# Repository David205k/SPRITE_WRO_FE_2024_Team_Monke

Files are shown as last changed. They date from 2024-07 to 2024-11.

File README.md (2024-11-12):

# SP RITE WRO FE 2024

## Team Information:


### Team ID:			`FE24_324_02`

### Team Name: 		`Team Monke` 

### Team Members: (from left to right)

- **Lim Jun Hong David <** [davidlimjunhong@gmail.com](mailto:davidlimjunhong@gmail.com) >
- **Chong Qi Yuan <** [Qiyuan146@gmail.com](mailto:Qiyuan146@gmail.com) >
- **Sachin Ilangovan <** [sachin5iconic@gmail.com](mailto:sachin5iconic@gmail.com) >

## Overview
#### Introduction	
Hello and welcome to Team `FE24_324_02` (Team Monke) GitHub repository. This is the GitHub repository for SINGAPORE World Robot Olympiad Future Engineers 2024. For WRO FE 2024, the competition focuses on Self-Driving Cars and in the challenge a robotic vehicle needs to drive autonomously on a parkours that randomly changes for each competition round.

In an ever-increasing automated world, the use of Autonomous Guided Vehicles (AGV) has become more prevalent. Furthermore, with recent improvements in Artificial Intelligence, specifically Computer Vision (CV), the integration of CV with AGVs is in high demand. Some possible applications with this integration include: 
-	Commercial: Self-Driving cars, housekeeping robots
-	Industry: Fully autonomous factory robots
-	Defence: Autonomous drones

This `README` will provide you with a quick overview of our process and resources we use for the competition. If you prefer a more thorough and detailed documentation of our journey for this competition, please check out our Engineering Journal that is also available in this GitHub repository `doc/`. Thank you

## Repository Content

- `doc/`:  Documentation
  - `Engineering Documentation.docx`
  - `Parts list`

- `models/`:
  - `Vehicle 3D Models` all ipt & iam files for vehicle design
    
  - `Engineering Drawings`
    - `Bottom Section Exploded view.png`
    - `Isometric view.png`
    - `Orthographic view.png`
    - `Top Section Exploded view.png`
    - `bottom disassembly.dwg`
    - `top disassembly.dwg`
    - `vehicle isometric view.dwg`
    - `vehicle orthogonal drawing.dwg`

  - `Disassembly Video`
    - `bottom disassembly.ipn`
    - `bottom disassembly.mp4`
    - `top disassembly.ipn`
    - `top disassembly.mp4`
  - `MONKE_BUST.stl`
  - `WRO_FE_2024.ipj.lnk`

- `ref/`: References for design idea & WRO_FE Rules, Field overview
  - `References.txt`

- `schemes/`: schematic diagrams of the electromechanical components illustrating all the elements used in the vehicle and how they connect to each other
  - `PCB Schematic Diagram.png`
  - `PCB ver.1.jpg`
  - `WRO_FE_PCB.fzz`
  - `WRO_FE_etch_copper_bottom.pdf`
  - `WRO_FE_schematic.fzz`
  - `front_PCB.png`
  - `Back_PCB.png`
  - `Soldered_PCB.jpg`

- `src/`: All python raspberry pi code to control software for all components
  - `main`
    - `main.py`
    - `pwmControl.py`
    - `tb6612fng.py`
    - `ultrasonicSensor_control.py`
  - `basic openCV/`:  basic programs using opencv and distance for objectDetection
    - `objectDetection.py`
    - `draw.py`
    - `read images.py`
    - `read videos.py`
  - `basic programs/`
    - `servo motor control ver.2.py`
    - `tb6612fng_motorDriver_control.py`

- `t-photos/`: 2 photos => Official Team photo and funny Team photo
  - `Official.png`
  - `Funny.png`

- `v-photos`: 6 photos of vehicle from all 6 side + overview for both SG and Türkiye Robot Designs
  - `WRO FE SG`  
    - `Top.png`
    - `Right.png`
    - `Left.png`
    - `Back.png`
    - `Front.png`
    - `Bottom.png`
    - `overview3.png`
  - `International Türkiye`
    - `Top.jpeg`
    - `Right.jpeg`
    - `Left.jpeg`
    - `Back.jpeg`
    - `Front.jpeg`
    - `Bottom.jpeg`
    - `Overview.jpeg`

- video: YouTube Video of vehicle demonstration in challenge
  - WRO FE SG
    - `Open Challenge.md`
    - `Obstacle Challenge.md`
  - International Türkiye
    - `Open Challenge.md`
    - `Obstacle Challenge.md`

- .gitignore: gitignore file
- README.md: This file

#### Hardware used
| Hardware | Description | Price (SGD)|
|---|---|---|
| Raspberry Pi 4 Model B | Control unit | $82.99 |
| MG996R Servo Motor | Steering actuator | $10.20 |
| 12v 380rpm 1.4kgcm Brushed DC Motor/ <br> DC 12V 1000RPM Gear motor | Main actuator | $19.64 |
| Full Metal Differential Gear set| Differential gear | $10.68|
| TB6612FNG Motor Driver | DC motor driver | $13.95 |
| LM2596 3A Buck Module with Display | DC voltage step down regulator | $4.96 |
| Raspberry Pi Camera Module 3 | Camera for Computer Vision | $46.61|
| US-015/ <br> VL53L1X Time of Flight sensor| High precision Ultrasonic Range Finder <br> / Long range, High precision IR Range Finder| $3.54 |
| HMC5883L | Triple Axis compass | $12.80 |
| Turnigy Lipo Pack 5000mAh 3S 25C W/XT-90/ <br> Turnigy Lipo pack 1300mAh 3S | Battery | $32.58 |
| 80mm Plastic Wheels SPG30/SPG50 | Main Driving wheel | $1.78 |
| Small Plastic Wheel | 34mm Steering Wheel | $2.00 |
| Ball Bearing | 6x13x5mm ball bearing | $3.41 |
| Printed Circuit Board | Custom PCB for mounting components | $8 |

For links to website for purchase of components, visit our either our /partslist or /engineering journal

## Overview of Robot
### WRO FE SG:
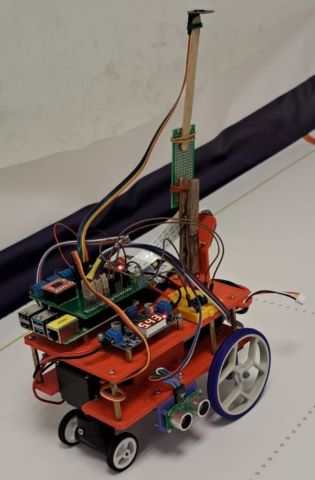
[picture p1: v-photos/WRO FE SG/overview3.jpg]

### WRO FE International Türkiye:
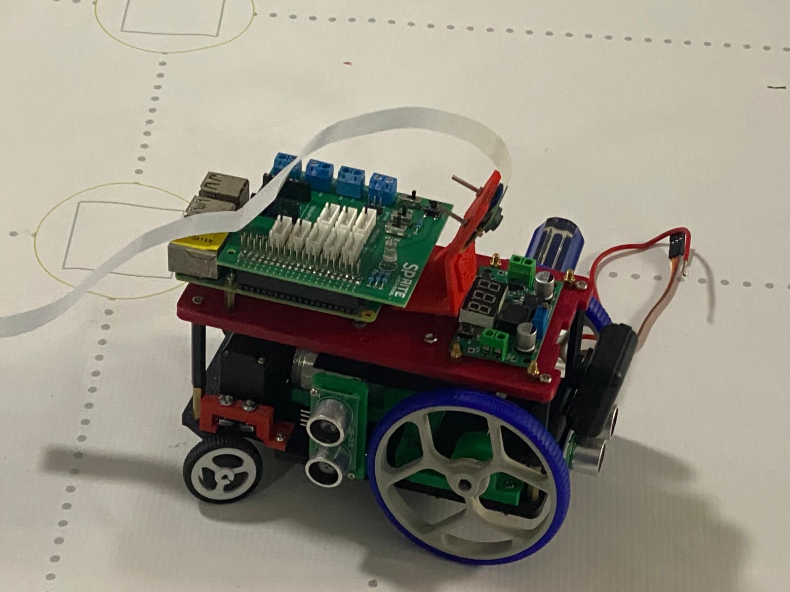
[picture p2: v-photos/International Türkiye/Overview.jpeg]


### Chassis
#### Steering
Originally, our robot featured a tricycle steering design. Where the steering is done directly by the servo turning (like a bicycle). This allowed us to simplify the steering design and also achieve tighter turns. 
However, we encountered some difficulties. Therefore we decided to swap to the ackerman steering for the internationals. 
This mainly offered advantageous in steering robustness, control and stability. However, this came at the cost of a more complex mechanism and a larger turning radius. 
#### Driving
Our robot is using a standard differential gear drive system, where 1 DC motor powers both wheels via a differential gear. A differential gear is used to prevent skidding and offer more stability and control. 

### Sense
Computer Vision: Our robot uses a Raspberry Pi to perform OpenCV computer vision to enable detection and avoidance of the obstacles. 
Distance Sensing: Our robot uses Time of Flight/Ultrasonic sensors to detect distances of walls, obstacles etc.
Vehicle direction: Our robot uses a Magnetometer Compass to obtain the bearing of the robot to enable accurate turns. 
By using this fleet of sensors, our robot is able to make informed decisions based on the information. 

For a more comprehensive overview of our design, proceed to our engineering document at `doc/`.

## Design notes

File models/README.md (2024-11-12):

This folder is dedicated to all hardware related CAD files. It is further split into 2 versions, the National and International version. 

This includes the Autodesk Inventor files and the STL files used for 3D printing components.

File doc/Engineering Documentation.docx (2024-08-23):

Team ID: FE24_324_02

Team Name: Team Monke

Team Members: Lim Jun Hong David, Chong Qi Yuan, Sachin Ilangovan

team monke engineering journal

WRO Future Engineers (FE)

ABSTRACT

The purpose of this competition is to design, fabricate, assemble, program, integrate and operate a self-driving car using computer vision.

This vehicle will be made using Raspberry Pi as its main controller and other off the shelf electronic components. The vehicle will also be operated as a steering robot, similar to real life cars.

Upon completion of this project, the vehicle should be able to navigate effectively between obstacles using sensor fusion and computer vision.

A copy of this Engineering Journal can also be found on GitHub (https://github.com/David205k/SPRITE_WRO_FE_2024_Team_Monke)

Other notes that we took are also found in the doc/ subdirectory.

1. Introduction
2. Design
- Hardware Overview
- Mobility Management
- Power and Sense
- Obstacle Management
- Code Style Guidelines
3. Fabrication
4. Assembly
5. Programming
6. Final Build
7. Conclusion

# Introduction

# System Architecture

## Hardware

## Software

# Development Process

# Results

# Conclusion

# References

# Appendix A

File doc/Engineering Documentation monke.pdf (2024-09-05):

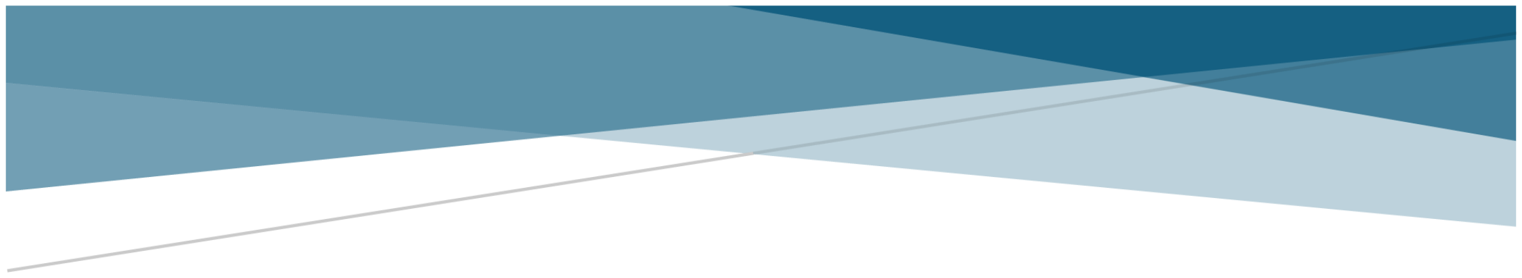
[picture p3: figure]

Team ID: | FE24_324_02
Team Name: | Team Monke

Team Members: Lim Jun Hong David, Chong Qi Yuan, Sachin Ilangovan

# TEAM MONKE ENGINEERING JOURNAL

## WRO Future Engineers (FE)

ABSTRACT
The purpose of this competition is to design, fabricate, assemble, program, integrate and operate a self-driving car using computer vision.
This vehicle will be made using Raspberry Pi as its main controller and other off the shelf electronic components. The vehicle will also be operated as a steering robot, like real life cars.
Upon completion of this project, the vehicle should be able to navigate effectively between obstacles using sensor fusion and computer vision.

A copy of this Engineering Journal can also be found on GitHub (https://github.com/David205k/SPRITE_WRO_FE_2024_Team_Monke) Other notes that we took are also found in the doc/ subdirectory.

## Contents

## INTRODUCTION

Project Background

In an ever-increasing automated world, the use of Autonomous Guided Vehicles (AGV) has become more prevalent. Furthermore, with recent improvements in Artificial Intelligence, specifically Computer Vision (CV), the integration of CV with AGVs is in high demand. Some possible applications with this integration include:

- Commercial: Self-Driving cars, housekeeping robots
- Industry: Fully autonomous factory robots
- Defence: Autonomous drones
Objectives

This project aims to create a self-driving car using Computer Vision via OpenCV and a Raspberry Pi camera. This will be assisted using Ultrasonic sensors to accurately identify distances. Furthermore, magnetometers will be used to determine the heading of the AGV to further refine turns overall sensor integration.
Scope of project

This project will be done using a Raspberry Pi. Therefore, design and fabrication of all components will be required. Integration of electronic components such as sensors, motor drivers, motors etc will also be required.

## HARDWARE

HARDWARE OVERVIEW

Description | Brand | Remarks | Quantity | Details
Servo Motor | | Steering Actuator | 1 | MG996R
12v 380rpm 1.4kgcm Brushed DC Motor | | Main Actuator | 1 | 12v 380rpm 1.4kgcm
Full Metal Differential Gear Set | | Differential Gear and Driver Gear for Robot rear shaft | 1
Raspberry Pi 4 Model B | Raspberry | Main Control Board | 1
High precision Ultrasonic Range Finder | | Ultrasonic Sensors | 3 | US-015
Raspberry Pi Camera Module 3 | Raspberry | Camera | 1
Motor Driver | | Motor Drivers | 1 | TB6612FNG
Ball Bearings | | Ball Bearings | 1 | 6x13x5 mm
Plastic Wheels | | Driving Wheels | 1 | 80mm
Small Plastic Wheels | | Steering Wheels | 1 | SPG330/SPG50 (80mm)
HMC5883L Module Triple Axis compass | | Triple Axis compass | 1 | HMC5883L
Lipo Pack | Turnigy | Power Supply | 1 | 5000mAh 3S 25C W/XT-90
LM2596 3A Buck Module with Display | | Voltage regulator | 1 | LM2596 3A
Custom designed PCB | | Integrate other components together | 1
NO Push button | | Push button to start/stop robot | 1
1k ohm resistor | | Resistor for push button | 1
220-ohm resistor | | Resistor for LEDs | 3

RGB cathode LED | RGB LED for display | 1
Switch | Turn on/off controller and motor | 2
Screw terminal | Connect battery and motor | 4

## OVERALL VEHICLE DESIGN

## Size

Our robot is at a shorter than the depth of the parking lot. This allows us to drive directly into parking, without the need to do parallel parking. A problem we encountered while doing such a design was that the physical components such as servo motor, differential gears and DC motor combined were too long. Therefore, we had to custom print a differential gear axle that was shorter.

## Component layout

Our robot has 3 layers available for mounting. The bottom layer is used mainly for actuation. The DC motor, differential and steering axle is at the bottom layer. Due to the large size of the batteries, the 2nd layer is dedicated to the batteries with a small part mounting the servo motor. The final top layer has the rest of our electronics such as the Raspberry Pi, the custom-made PCB, camera and voltage regulator. These components were placed here for easy access.

## MOBILITY MANAGEMENT

## Chassis

For our chassis, our team decided to use a tricycle approach instead of typical Ackerman steering configuration. This is reducing the steering mechanism’s complexity while also reducing turning radius. his approach simplifies the steering mechanism while significantly reducing the turning radius, allowing for sharper angles and tighter manoeuvrers. This is particularly useful in our scenario where obstacles and pillars are closely spaced, requiring the vehicle to make quick and precise turns in either direction. Our design deviates from traditional tricycle layouts by placing the steering mechanism at the rear and the differential gear system at the front. This configuration is intended to optimize the length of the robot while accommodating the ultrasonic sensors. One of these sensors is mounted at the front, where it benefits from existing space around the differential gear system. Placing the sensor here avoids the need for additional material spacing, which would have been necessary if it were positioned near the steering mechanism.
The rear-wheel steering allows the vehicle to pivot more sharply around the front wheels, making it extremely agile in tight spaces. This enables more precise adjustments when navigating through an obstacle course which is particularly useful when passing through obstacles.

## Steering

Using a tricycle approach, our vehicle uses a single steering axle, controlled directly by a servo motor. This allows us to simplify the steering design while also allowing a wide range of steering angles for optimal mobility.
The servo motor will be the steering mechanism of our vehicle. For our steering mechanism we only required the turning axle to turn about 90 degrees
The MG996R servo motor can rotate 90 degrees and has been tested to be more accurate than its previous models.

## Actuation

DC Motor & Full Metal Differential Gear Set:
At the start of planning and design we initially were planning on using a 3V - 6V Dual Axis TT Gear Motor but after some thought we realised that it would not be very efficient and logical as that motor would not have enough power to be able to move the vehicle at a required speed and would be very slow and would also be difficult to implement a differential gear set to it.

So, after some thought and research we landed on the 12v 380rpm 1.4kgcm Brushed DC Motor. From research, this motor provides higher speed and higher torque. The motor is mounted with a 30:1 gearhead that can produce 137mN.m torque with 380RPm rated 1A,12V. A full metal differential gear set is connected to the DC motor.

The use of differential gears allows the wheels to move at different rpms. They also serve a purpose of speed reduction while effectively transmitting torque. This allows smooth turning and cornering and optimal power distribution by dividing the force equally between them but still allowing them to follow paths of different length when turning.

The main function of the differential is to allow the wheels to turn at different rpms. In a scenario where the vehicle must turn right, the left wheel must move a longer distance than the right wheel, which means that the left wheel needs to rotate at a higher speed. This is where a differential would be useful.

DC Motor: | 137mNm, 380rpm
Mass of robot: | 1.45kg
| Torque/kg = 94.5mNm/kg
| Power to weight ratio = 1255W/kg
| Max speed of 380 rpm = 1591.7mm/s

The motor we chose provides sufficiently high RPM and torque whilst not being too expensive. Our needs as calculated above, are sufficiently met with a relatively controllable yet high max speed and sufficient power to weight ratio for a small robot.

Motor driver: TB6612FNG
To control our DC motor actuator, we require a motor driver. We chose the TB6612FNG since it met our power and actuation needs. It outputs 1.2A at up to 15V. This matches well with our motor which can take from 1A – 5A at 12V. This allows us to provide sufficient power to our motor while not overloading it or overspending on excessive equipment.
In addition to forward and reverse control, the TB6612FNG offers braking and standby modes. The brake mode quickly stops the motor, while the standby mode reduces power consumption when the motor is not in use.

## POWER AND SENSE

## Power

Consumption

DC motor: | 1A, 12V at max load
Raspberry Pi 4: | 5V, 3A
Battery: | 5000mAh 3cell 25C, 11.1v

At maximum load, the battery provides sufficient power with a comfortable excess. The main component consuming power is our controller, the Raspberry Pi at 3A. Power to the Raspberry Pi from the battery is first regulated by the Buck module to prevent overload. As for our main actuator, the DC motor, is controlled by the Motor driver which receives power directly from the battery. This is because the Motor Driver’s VM is rated at 15V, higher than the battery’s. This allows us to receive maximum power to the main actuator without any loss of power.

Servo Battery: | 1000mAh, 7V
Servo: | 7.2V max

We use a separate Servo battery since our main battery provides to much power to the servo even with a regulator.

## Sense

Controller: Raspberry Pi Module
We chose to use a Raspberry Pi instead of an Arduino because a Raspberry Pi is an operating system, allowing us to run more complex operations. Additionally, Raspberry Pi and Arduino are both popular choices in robotics projects, providing extensive online resources for support. We're also using VNC Viewer to remotely access and control the Raspberry Pi, which adds convenience and flexibility during development and testing. Moreover, since we plan to utilize the OpenCV library, which requires Python, Raspberry Pi is the ideal choice for our project.
- Processing Power: The Raspberry Pi 4 Model B is equipped with a quad-core ARM Cortex-A72 CPU, providing significantly more processing power compared to other microcontrollers like Arduino. This allows it to run complex algorithms, such as computer vision or machine learning, in real-time.
- Versatility and Flexibility: the Raspberry Pi 4 offers access to a vast ecosystem of software and programming languages. This flexibility enables easy integration with various sensors, cameras, and software libraries needed for advanced robotics tasks.
- Image Recognition with OpenCV: The Raspberry Pi 4 supports the Raspberry Pi Camera Module, which enables image recognition tasks. Coupled with OpenCV, a widely used library for computer vision, the Raspberry Pi 4 can perform real-time image processing, object detection, and visual navigation. This capability allows your robotic vehicle to recognize objects, track movements, and make decisions based on visual inputs, providing a significant advantage in a dynamic environment.
- Connectivity: Built-in Wi-Fi and Bluetooth on the Raspberry Pi 4 are crucial for wireless communication, remote control, or IoT integration, which is particularly useful in competitions for connecting multiple devices. This is especially useful when coding and troubleshooting.
- Multiple I/O Options: The Raspberry Pi 4 offers multiple GPIO pins, USB ports, and HDMI outputs, allowing for interfacing with a wide range of peripherals, sensors, and modules without needing additional hardware.
- I2C BUS connection: The Raspberry Pi 4 provides SDA and SCL connection for I2C. This is because both the Gyro (mpu6050) and Magnetometer (TB6612FNG) use I2C. By using the I2C bus, the gyro and magnetometer will have their unique I2C bus address, preventing data overlap. I2C is used for these components since it allows for data exchange between microcontrollers with minimum wiring. Ultrasonic Sensor: US-015
For our vehicle, we have strategically placed three ultrasonic range finders at the front, left, and right sides. These sensors play a crucial role in manoeuvring by helping the vehicle avoid obstacles like traffic pillars and maintaining a safe distance from the external and internal boundary walls of the field. The side sensors are particularly useful for detecting the side walls, ensuring the robot stays centred. At the front, we've positioned both a camera and an ultrasonic sensor to detect obstacles and measure distances effectively. We also place the Ultrasonic sensor below the robot so that it can reliably detect the walls.

We're using the US-015 model, which offers a measuring range from 2 to 400 cm with an accuracy of up to 1 mm. Its stability and consistency make it ideal for precise robotics operations like this one.

Camera: PI Camera
The Raspberry Pi Camera is mounted on the front top of the vehicle, serving as the 'eyes' of the robot. Its primary function is to detect obstacles and identify their colour, which allows it to send signals to the robot on which direction to turn. By placing the camera in this position, it optimizes the vehicle's ability to efficiently detect obstacles.

We chose the Raspberry Pi Camera Module 3 as it is the latest model, offering advanced features such as phase detection, which facilitates image recognition. This capability allows the system to differentiate between green and red pillars, guiding the vehicle's directional turns accordingly. Additionally, the camera supports various default modes, including 480p at 120 frames per second. With such a high frame rate, our robot can receive near-instantaneous information, ensuring responsive and accurate movement.

Magnetometer: HMC5883L Module Triple Axis compass

We are using the HMC5883L is a magnetometer sensorto derive the direction of our robot. This will enable the robot to be able to make more refined movements. For example, the robot will be able to determine how many rounds it has done.
The main reason we chose the HMC5883L was due to its accessibility and price and our usage purpose. A gyroscope was not suitable since we required a direction heading and a gyroscope would require algorithms and further modifications to achieve that. The HMC5883L allowed us to obtain the direction of the robot at a relatively low price.

Integration: Printed Circuit Boards
To integrate all our sensors and microcontrollers, we required something to combine them together and provide the necessary power with I/O connection. Therefore, we chose to use a custom printed PCB. Two other options were available to us as well. A breadboard or a perforated board. Breadboards was not a very long-term solution, and breadboard connections are not very secure, particularly on a moving robot. Not to mention mounting of the breadboard would also cause issues. Perforated boards offer more secure connections, but the soldering of all connections will be time consuming. Furthermore, we wanted a solution that could last and could be reused for other projects. Therefore, we chose to use a PCB since it allowed us to have secure connections, enable stacking of header pins on the Raspberry Pi and less soldering required. This also provided a valuable learning experience in how to PCB design.

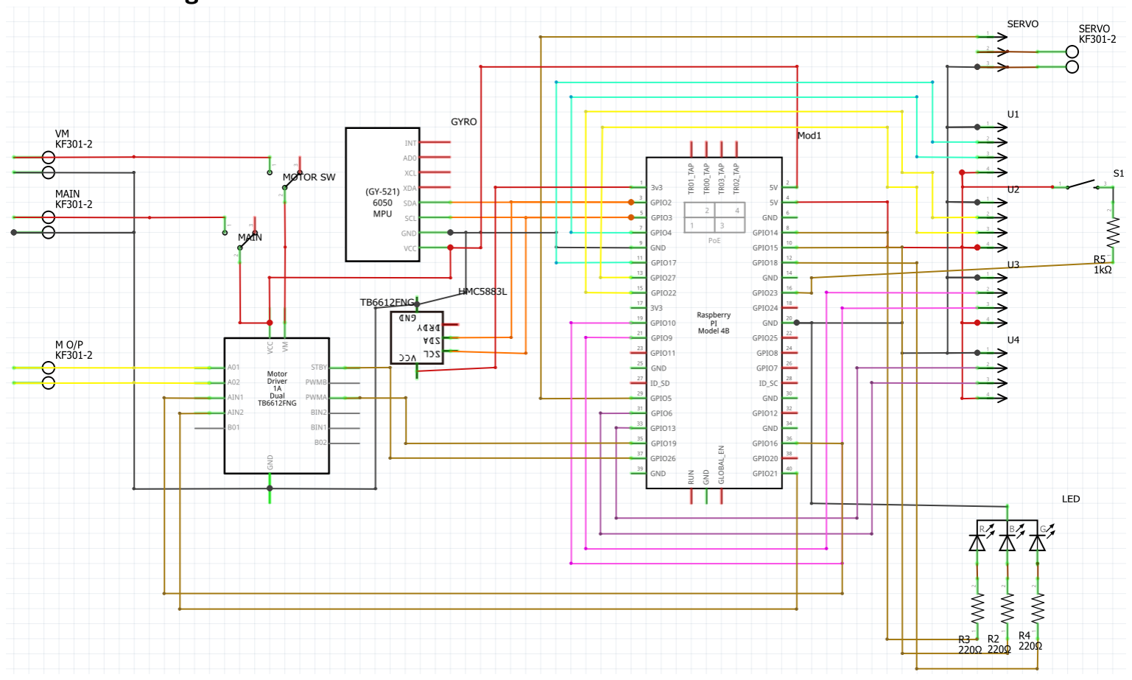
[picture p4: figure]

Schematic Diagram:

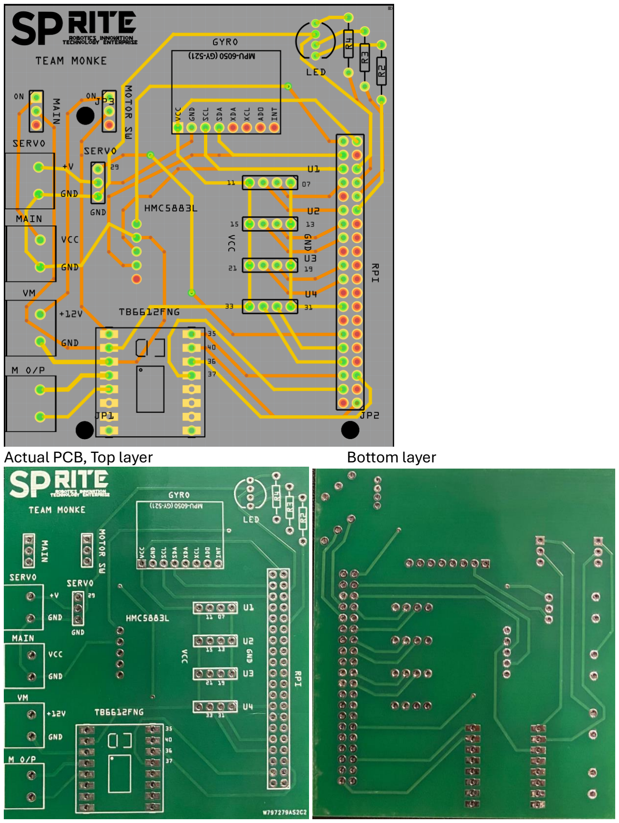
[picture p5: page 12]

Actual PCB, Top layer | Bottom layer

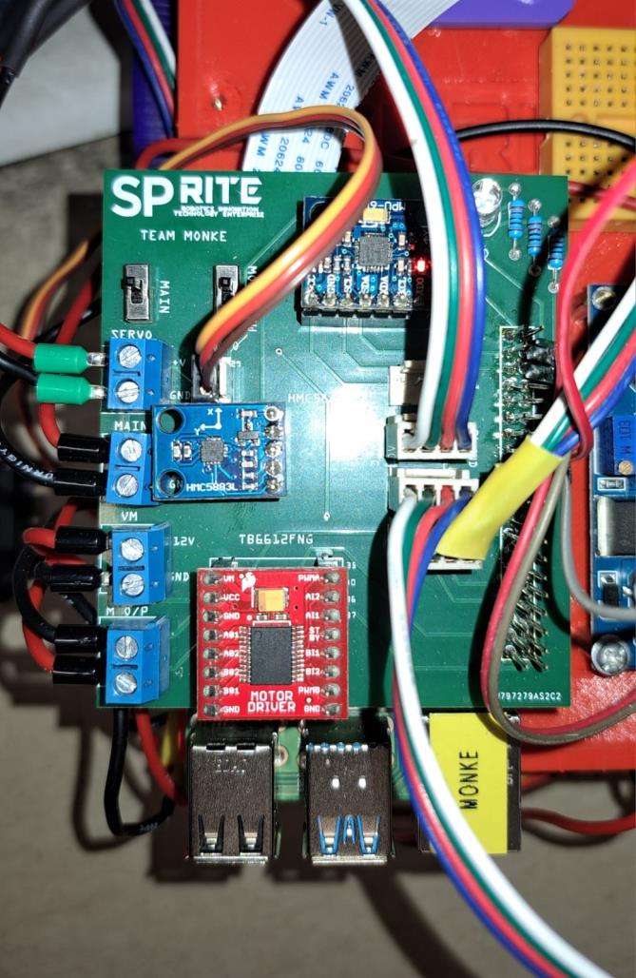
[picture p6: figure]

PCB with all components mounted on our robot

## DEVELOPMENT MILESTONES

## Fabrication

PCB

Old PCB
Visible from the image above, there were multiple improvements to be made to the PCB. For example, the screw terminals are the wrong size.

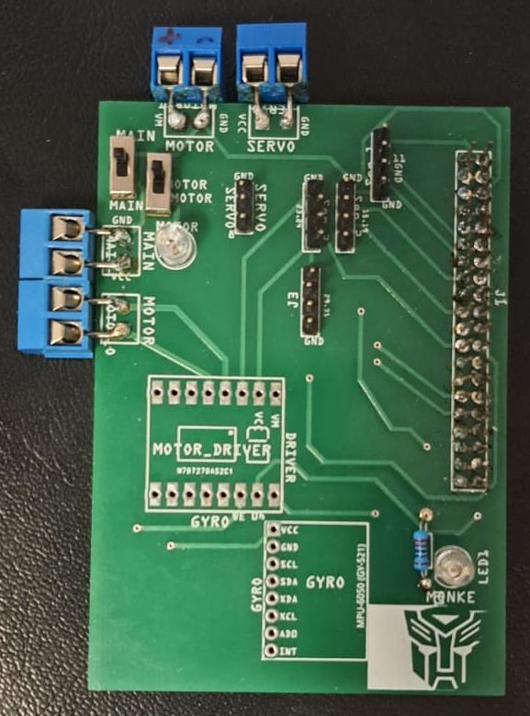
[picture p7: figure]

AGV

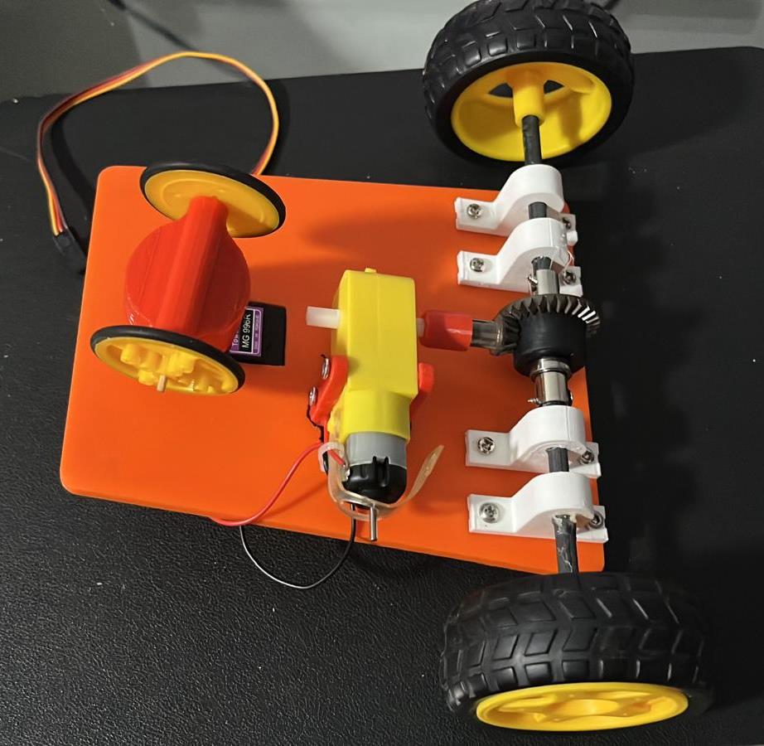
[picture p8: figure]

This is our very first AGV that we tried. This was meant as a proof of concept, testing out the differential gear drive and tricycle steering.

## Assembly

PCB
As our 2nd prototype, we used a breadboard to test out the motor driver. From insecure connections to messy wires, it was clear that we needed a PCB.

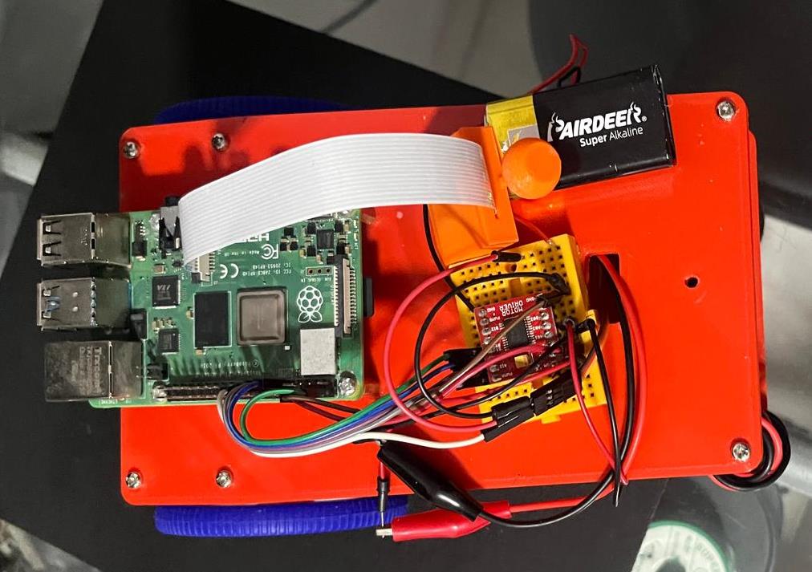
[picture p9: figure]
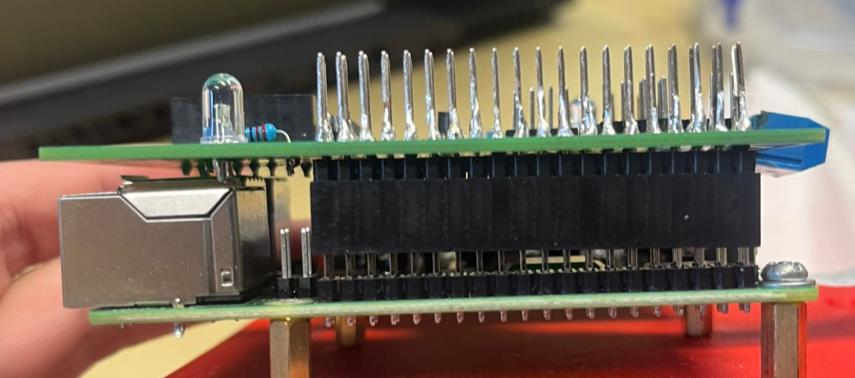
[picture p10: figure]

Upon assembling our PCB, we noticed that the Raspberry Pi’s USB and ethernet ports were blocking it.
AGV

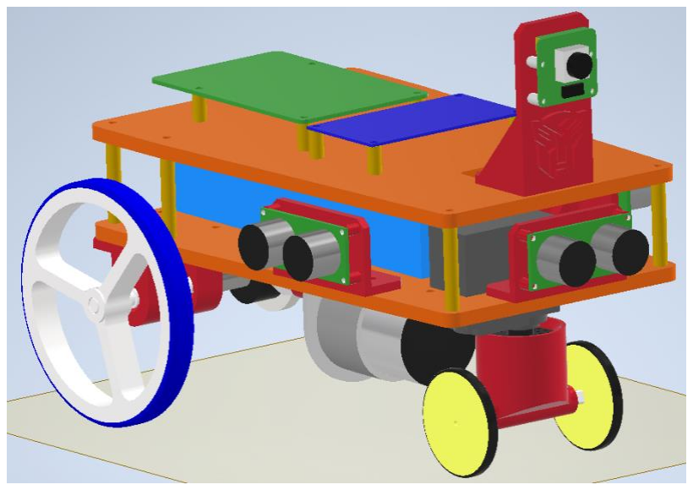
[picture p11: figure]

This is the 3D CAD file of our old AGV.
The robot is facing a different direction and is much longer than our current version.

As our final
prototype,
we started
integrating
the camera
and
OpenCV
control.

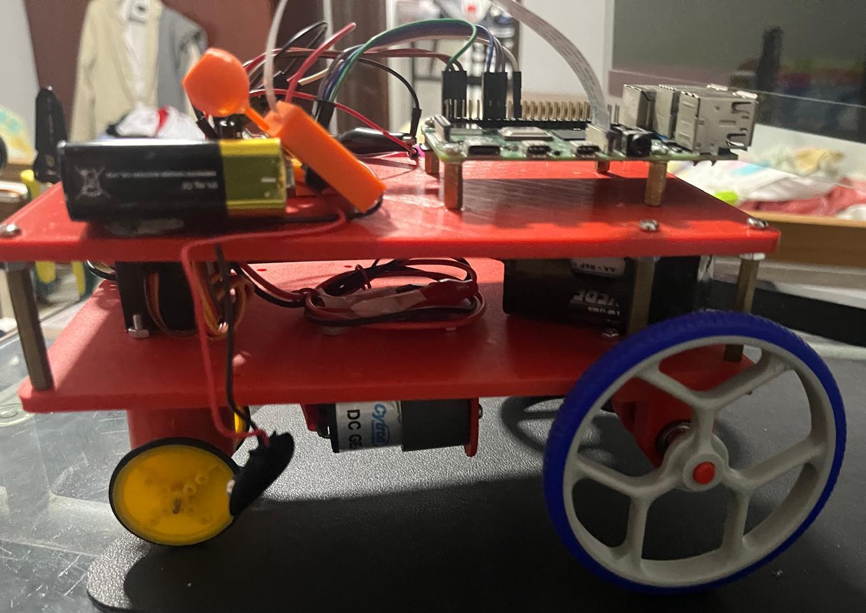
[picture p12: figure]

## Troubleshooting

Previously, we connected the servo motor directly to the battery. This caused the servo to overload and fry. Therefore, we are now using a smaller dedicated battery for the servo.
With our current steering configuration, our servo overload due to direct steering forces. When steering at sharp angles, the servo must exert a large amount of power and experiences forces of the robot pulling it forward.

## PSEUDO CODE

Open Challenge:

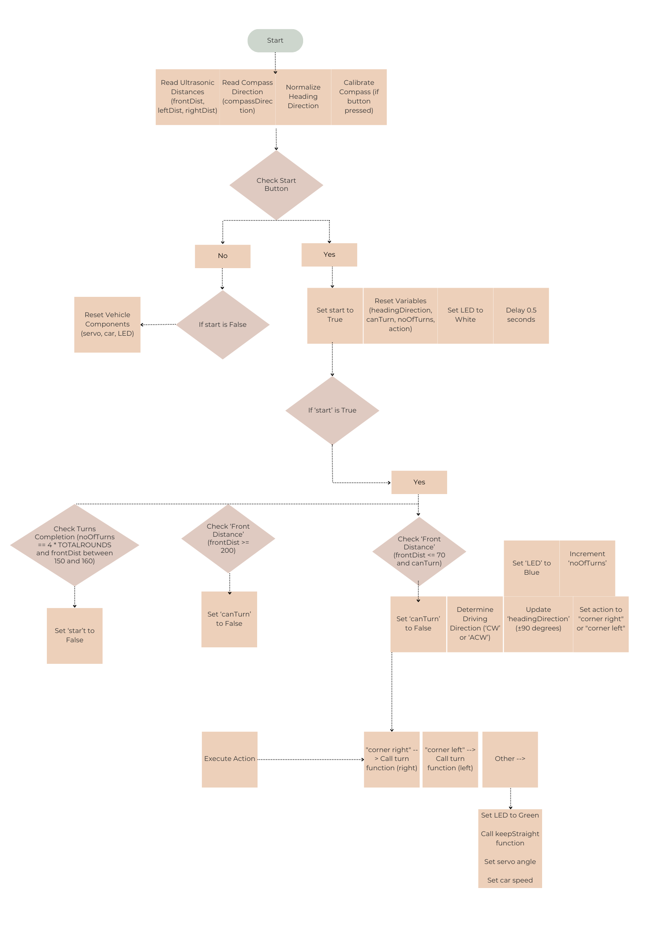
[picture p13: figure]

## CONCLUSION/IMPROVEMENTS

## Sensors

1) Instead of Ultrasonic sensors, we can use Lidar sensors instead. Lidar is much more consistent and accurate compared to ultrasonic sensors. Our team encountered some difficulties in the consistency of the Ultrasonic sensor.
2) A different camera can be used. Our current camera does not have very high frames at higher resolutions. This limits our object detection via computer vision.

## PCB

1) A push button can be added on the PCB so that we are able to start/stop the robot or give inputs during testing.

## REFERENCES

WRO FE Rule Book:
https://wro-association.org/wp-content/uploads/WRO-2024-Future-Engineers-Self-Driving-Cars-General-Rules.pdf (https://wro-association.org/wp-content/uploads/WRO-2024-Future-Engineers-Self-Driving-Cars-General-Rules.pdf)
VNC Viewer References:
https://www.google.com/url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 (https://www.google.com/url?rct=j&opi=89978449) https://youtu.be/ikUH_wOesIY?si=3h6Y2FHPOmsgjrJ-https://youtu.be/ocWZ9QFgvXk?si=nr7zo171_FX9tkB3
Programming References:
https://how2electronics.com/interfacing-hmc5883l-magnetometer-with-raspberry-pi/https://forum.arduino.cc/t/multiple-and-simultaneous-ultrasonic-sensor-controlling/26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 (https://forum.arduino.cc/t/multiple-and-simultaneous-ultrasonic-sensor-controlling/266009)
GitHub References:
https://github.com/World-Robot-Olympiad-Association/wro2022-fe-template

## APPENDIX A

Below are the images of our AGV
Bottom | Top

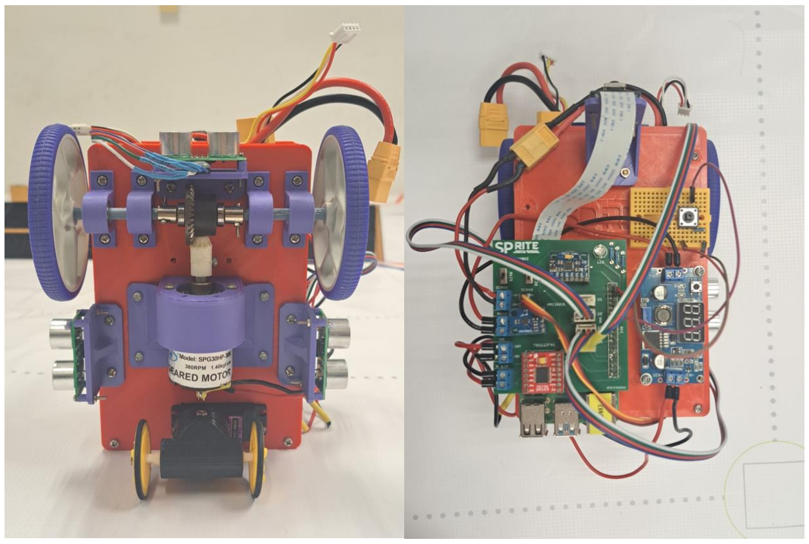
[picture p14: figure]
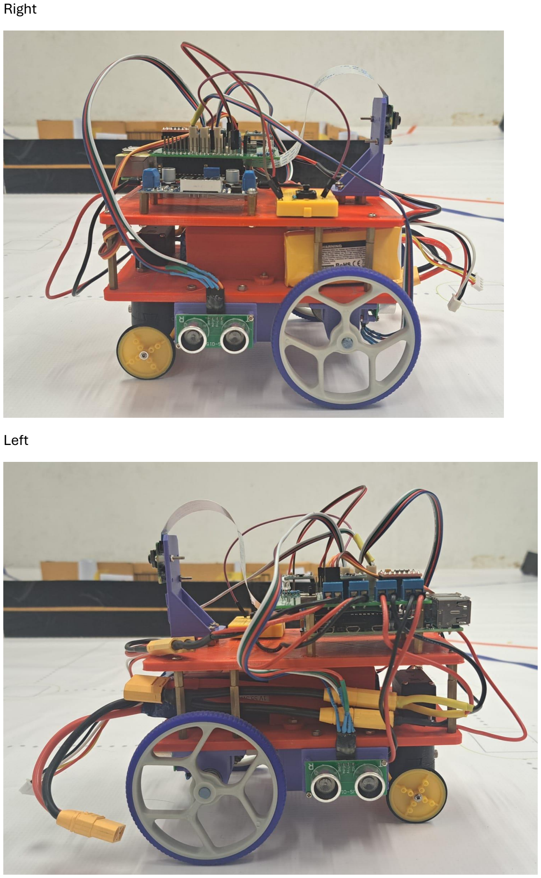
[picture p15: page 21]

Right

Left

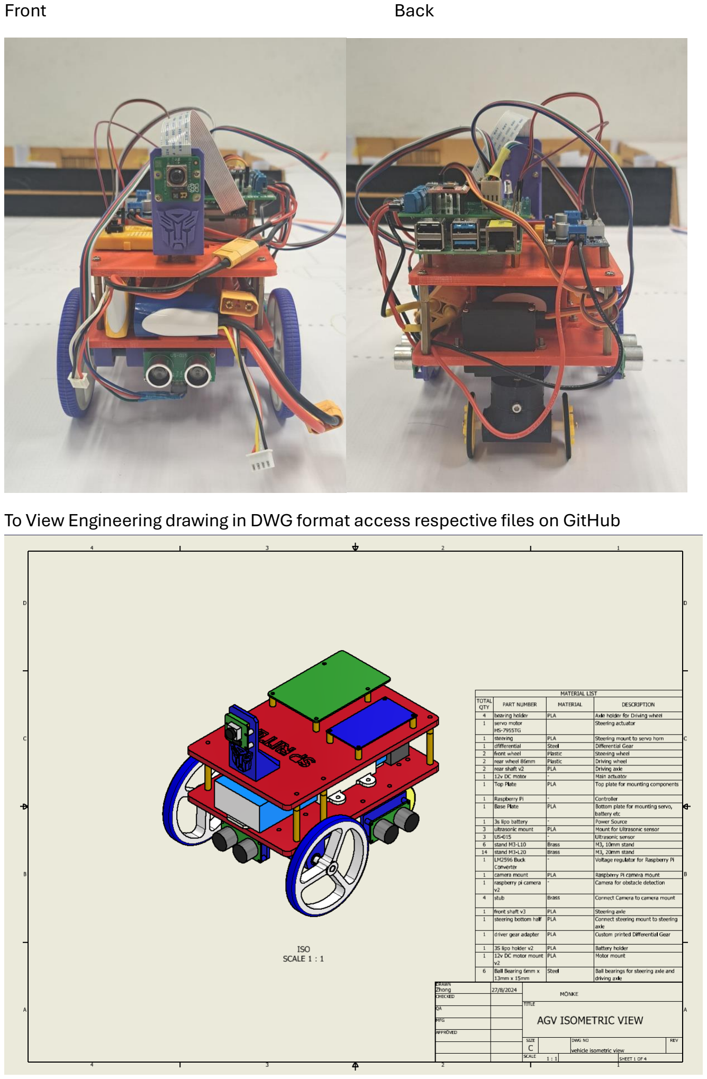
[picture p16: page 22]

Front | Back

To View Engineering drawing in DWG format access respective files on GitHub

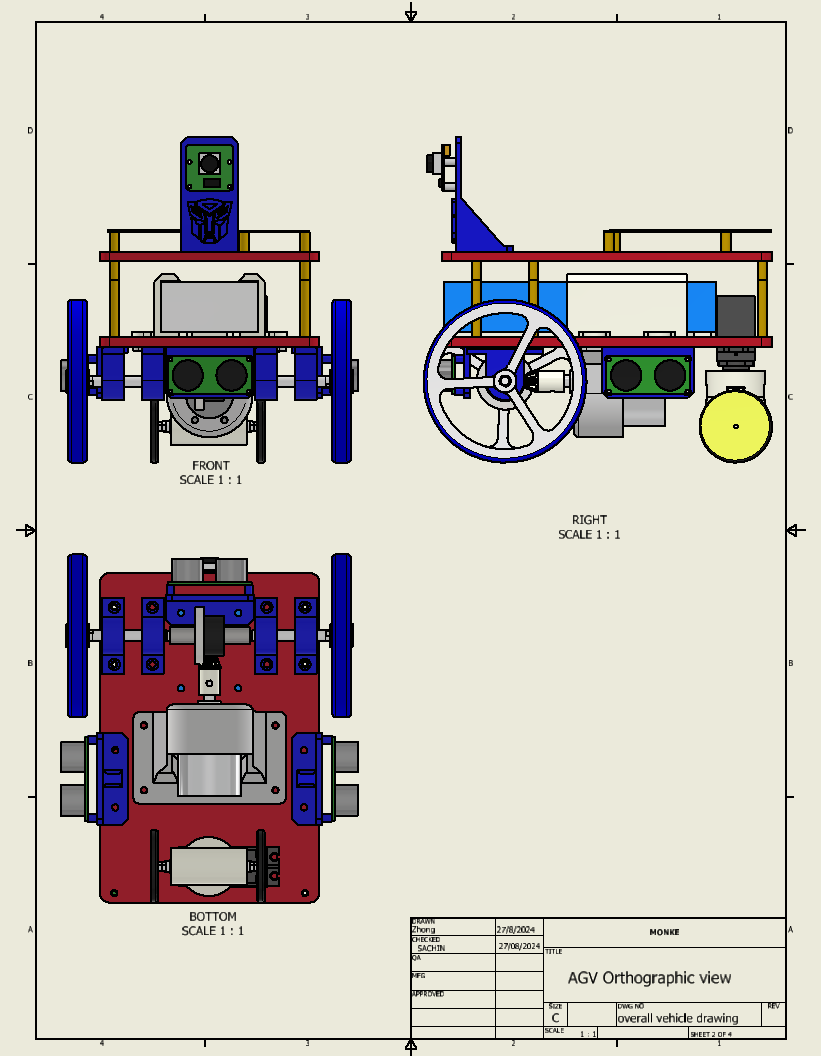
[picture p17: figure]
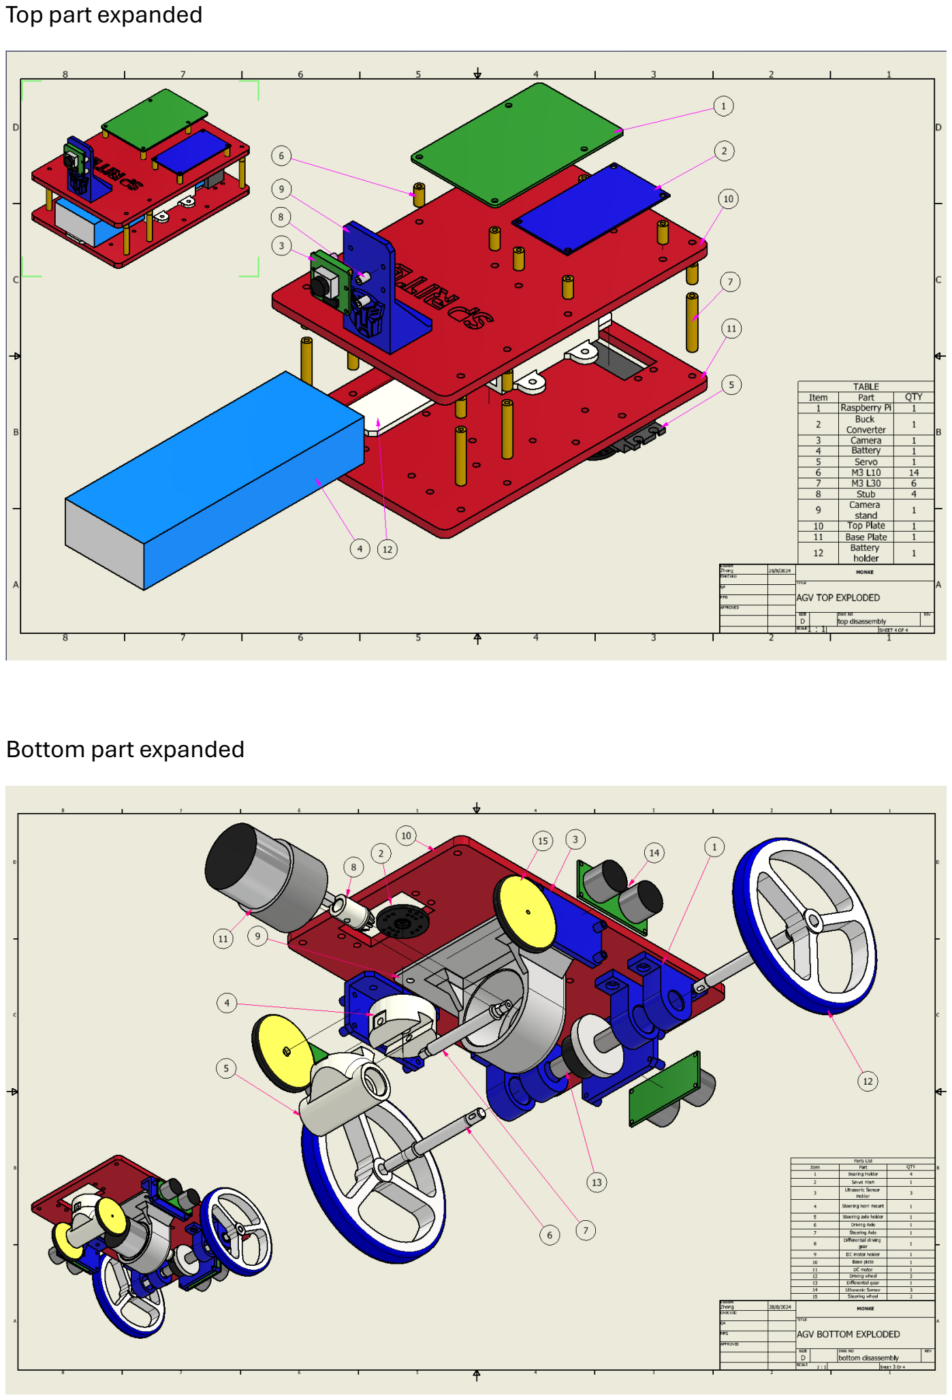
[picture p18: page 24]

Top part expanded

Bottom part expanded

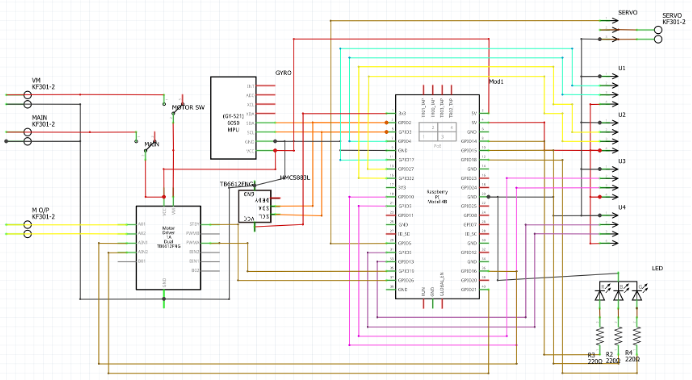
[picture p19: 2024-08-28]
schemes/PCB Schematic Diagram.png

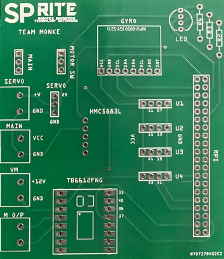
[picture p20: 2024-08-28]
schemes/front_PCB.png

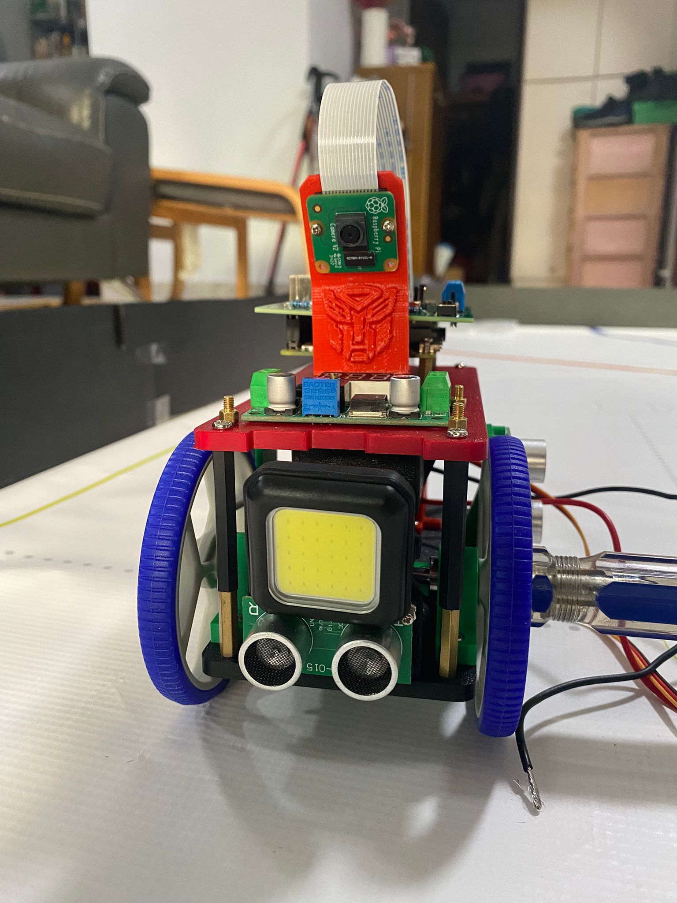
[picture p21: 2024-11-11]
v-photos/International Türkiye/Front.jpeg

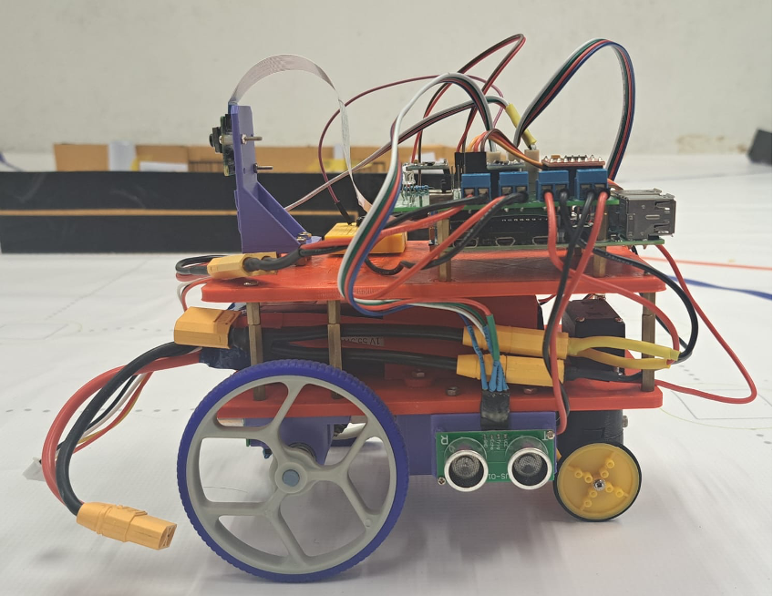
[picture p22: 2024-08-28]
v-photos/WRO FE SG/Left.png

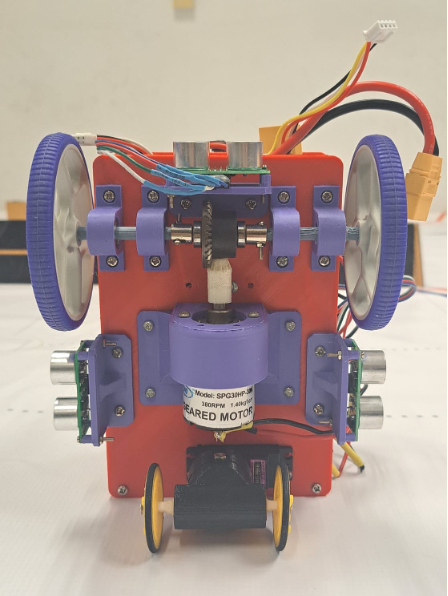
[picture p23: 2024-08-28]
v-photos/WRO FE SG/Bottom.png

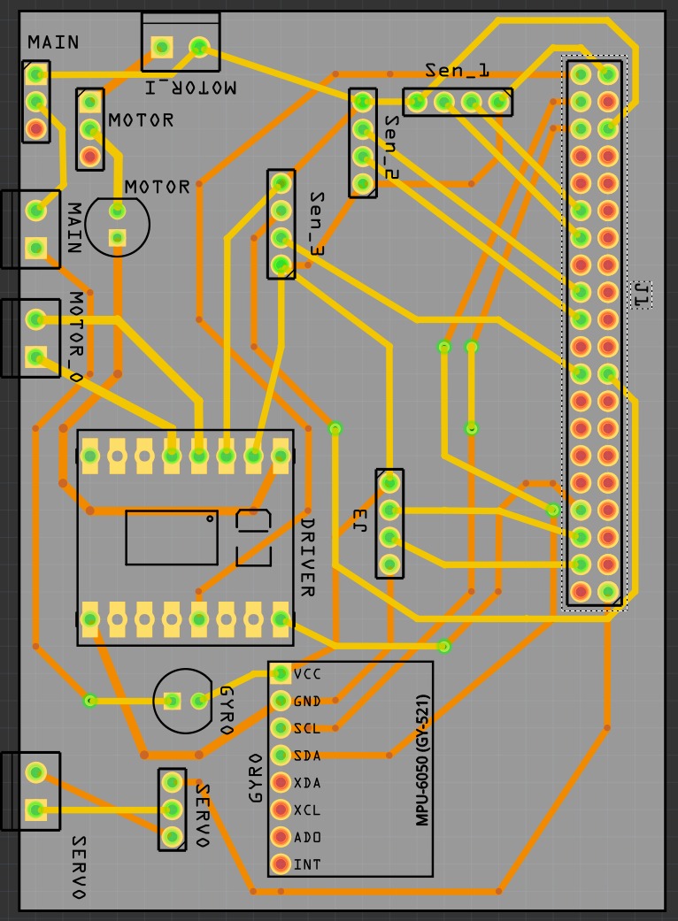
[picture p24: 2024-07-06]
schemes/PCB ver.1.jpg

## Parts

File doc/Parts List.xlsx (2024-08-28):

Description | Unit Price | Quantity | Source |  | Total Price | Remarks
12v 380rpm 1.4kgcm Brushed DC Motor | $19.64 | 1 | Cytron Tech | https://sg.cytron.io/p-12v-380rpm-1.4kgfcm-high-power-brushed-dc-geared-motor | $19.64 | Main Actuator
Servo Motor MG996R | $10.20 | 1 | Cytron Tech | https://sg.shp.ee/mt76Tnt | $10.20 | Steering Actuator
Full Metal Differential Gear Set | $10.68 | 1 | Shopee | https://shopee.sg/-Kesoto2-RC-Car-Differential-Replaces-Parts-Durable-Quality-Sturdy-Gear-Drive-Shaft-Spare-Parts-for-16101-16102Pro-16201Pro-Repair-Parts-Tru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 | $10.68 | Differential Gear and Driver Gear for Robot Rear Shaft
Raspberry Pi 4 Model B | $82.99 | 1 | Cytron Tech | https://sg.cytron.io/p-raspberry-pi-4-model-b-4-gb-and-kits | $82.99 | Main Control Board
5mp v1.3 Rapsbery Pi Camera | $6.99 | 1 | Shopee |  | $6.99 | 1st Camera Bought for Testing
TB6612FNG Motor Driver | $13.95 | 1 | SparkFun | https://www.sparkfun.com/products/14450 | $13.95 | Motor Drivers
High Precision Ultrasonic Range Finder US-015 | $3.54 | 4 | Cytron Tech | https://sg.cytron.io/p-high-precision-ultrasonic-range-finder-us-015 | $14.16 | Ultrasonic Sensors
Ball Bearings 6x13x5 mm | $3.41 | 1 | Shopee | https://shopee.sg/product/110868311/1947445015?d_id=a78bf&uls_trackid=501mi0gp009g | $3.41 | Ball Bearings
Front Wheels | $2.00 | 1 | Cytron Tech |  | $2.00 | Front Wheels
Plastic Wheel SPG30/SPG50 (80mm) | $1.79 | 2 | Cytron Tech | https://sg.cytron.io/p-12v-380rpm-1.4kgfcm-high-power-brushed-dc-geared-motor | $3.58 | Rear Wheels
HMC5883L Module Triple Axis Compass Magnetometer | $12.80 | 1 | Shopee |  | $12.80 | Compass 1
LM2596 3A Buck Module with Display | $4.96 | 1 | Cytron Tech | https://sg.cytron.io/p-lm2596-3a-buck-module-with-display | $4.96 | Voltage Regulator
Turnigy 5000mAh 3S 25C Lipo Pack W/XT-90 | $32.58 | 1 | HobbyKing | https://hobbyking.com/en_us/turnigy-battery-5000mah-3s-25c-lipo-pack-xt-90.html | $32.58 | Power Supply
GY-521 MPU6050 6DOF Accelerometer + Gyro | $3.75 | 1 | Cytron Tech | https://sg.cytron.io/p-gy-521-mpu6050-6dof-accelerometer-plus-gyro | $3.75 | Compass 2
Raspberry Pi Camera Module 3 | $46.61 | 1 | Cytron Tech | https://sg.cytron.io/p-raspberry-pi-camera-module-3-12mp-with-auto-focus-lens | $46.61 | Camera
TCS3200 Colour sensor | $11.79 | 1 | Cytron Tech | https://sg.cytron.io/p-colour-sensor-module | $11.79 | Colour Sensor
Custom designed PCB |  | 1
Noramlly Open Push button |  | 1
1k ohm resistor |  | 1
20 ohm resisior |  | 3
RGB cathode LED |  | 1
switch |  | 2
XT90 Connectors |  | 4
XT60 Connectors |  | 1
Total Cost (Excluding Shipping) |  |  |  |  |  | $280.09

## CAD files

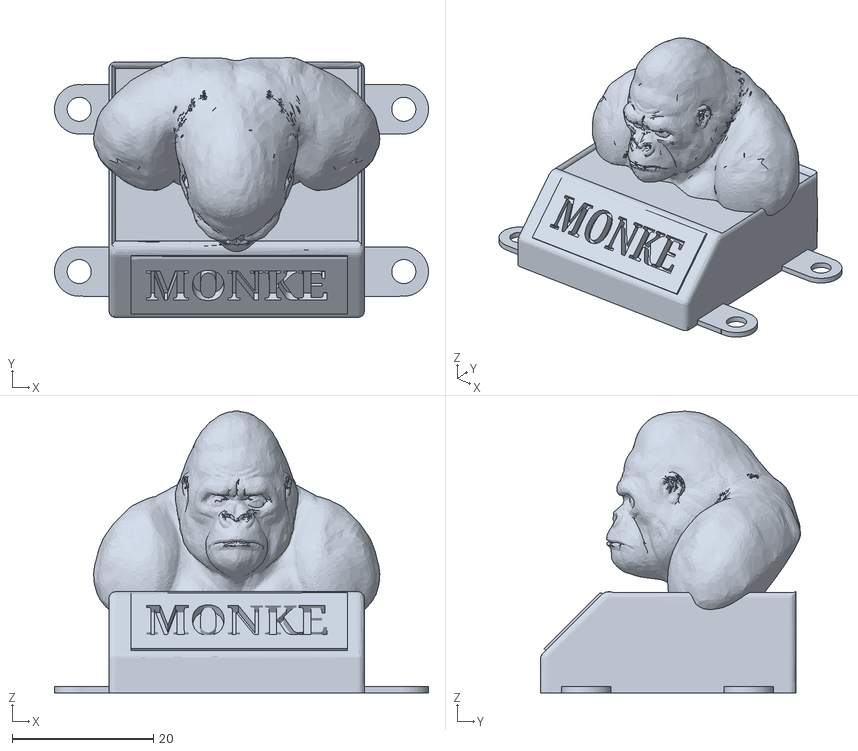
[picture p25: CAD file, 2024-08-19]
models/MONKE_BUST.stl
53.0 x 36.8 x 39.9

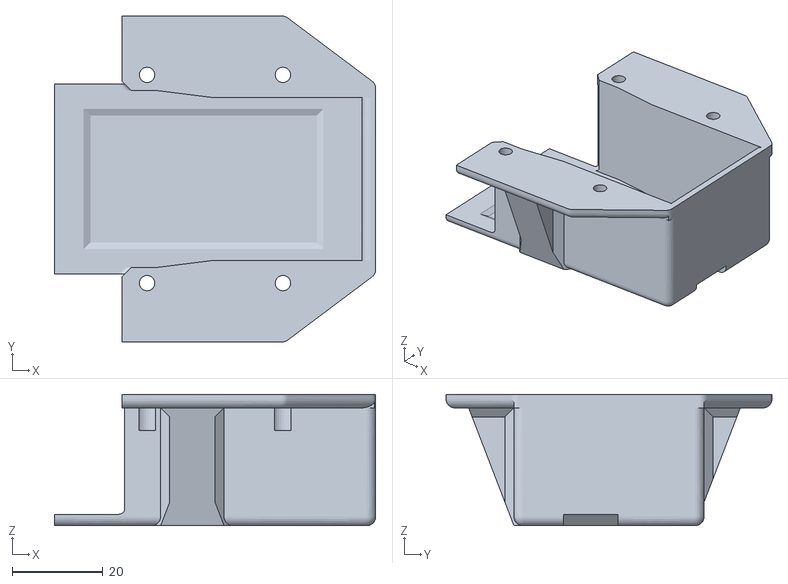
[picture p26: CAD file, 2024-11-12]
models/New robot (TR)/STL files/Battery Mount V2.stl
71.0 x 72.0 x 29.0

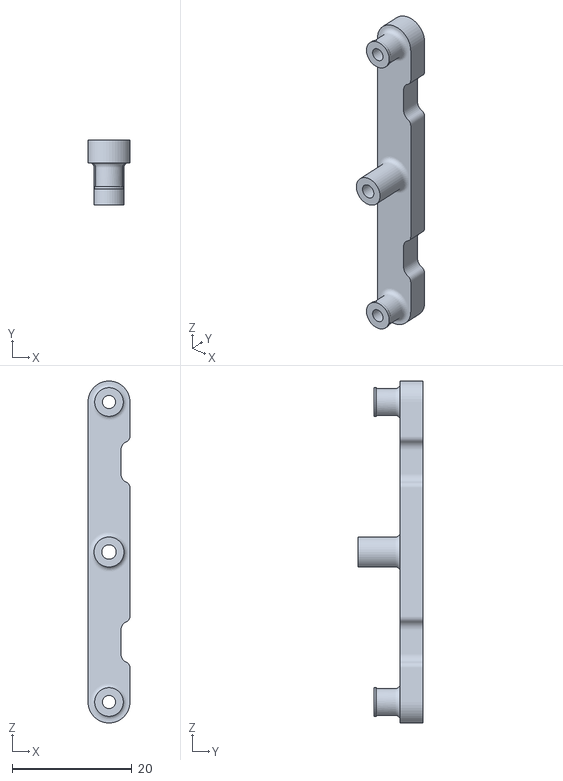
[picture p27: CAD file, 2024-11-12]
models/New robot (TR)/STL files/ActuatorLink.stl
7.00 x 10.8 x 57.0

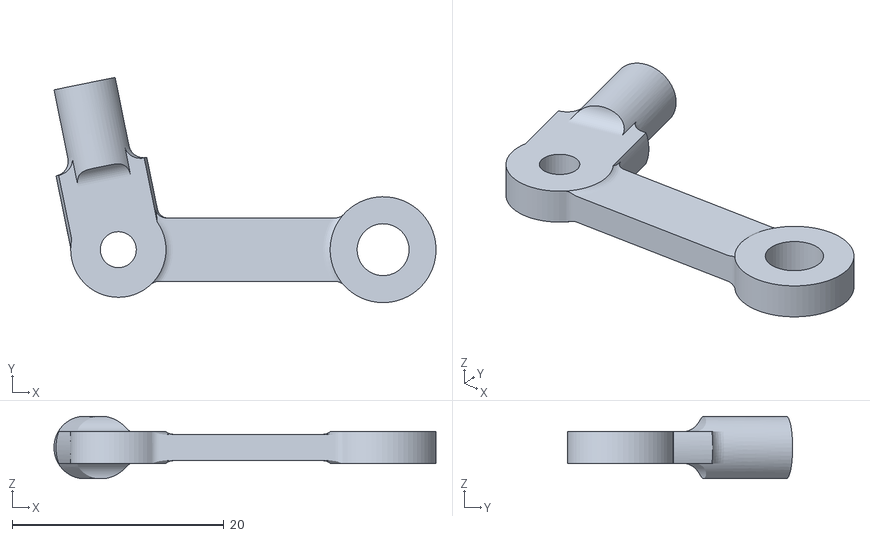
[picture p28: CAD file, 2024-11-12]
models/New robot (TR)/STL files/Wheel_Pivot.stl
36.1 x 21.3 x 5.90

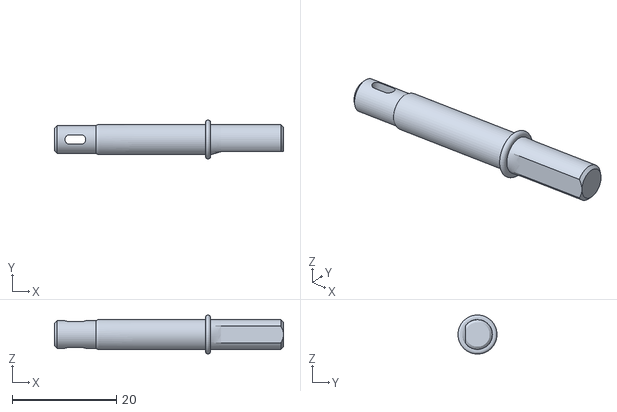
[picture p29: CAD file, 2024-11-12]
models/New robot (TR)/STL files/rear shaft v2.stl
44.0 x 7.50 x 7.49

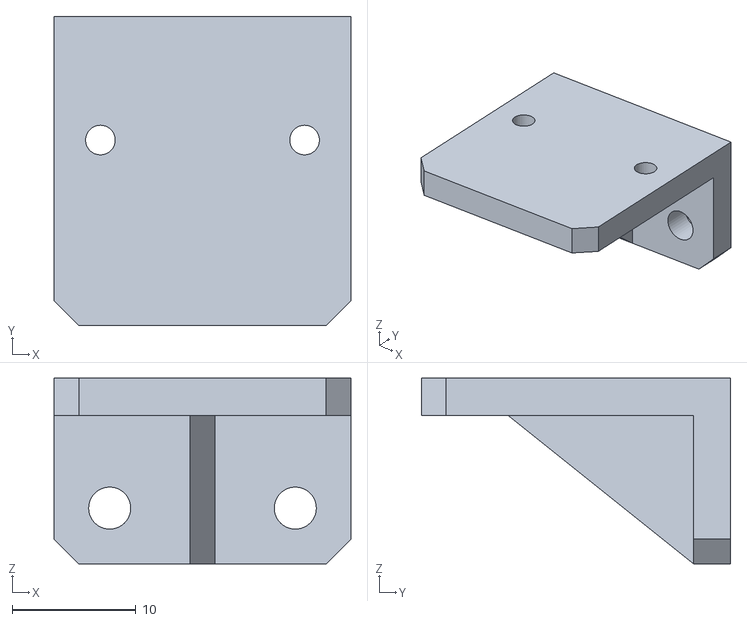
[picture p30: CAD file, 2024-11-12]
models/New robot (TR)/STL files/Vertical TOF mount.stl
24.0 x 25.0 x 15.0

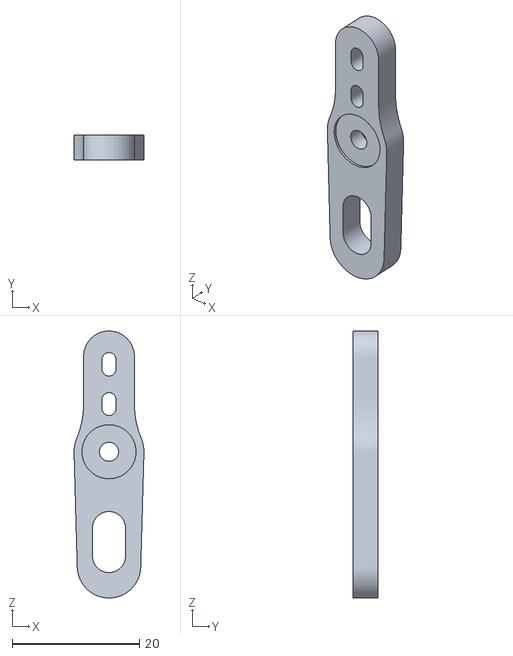
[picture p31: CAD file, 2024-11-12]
models/New robot (TR)/STL files/Servo steering actuator v2.stl
11.0 x 4.00 x 42.0

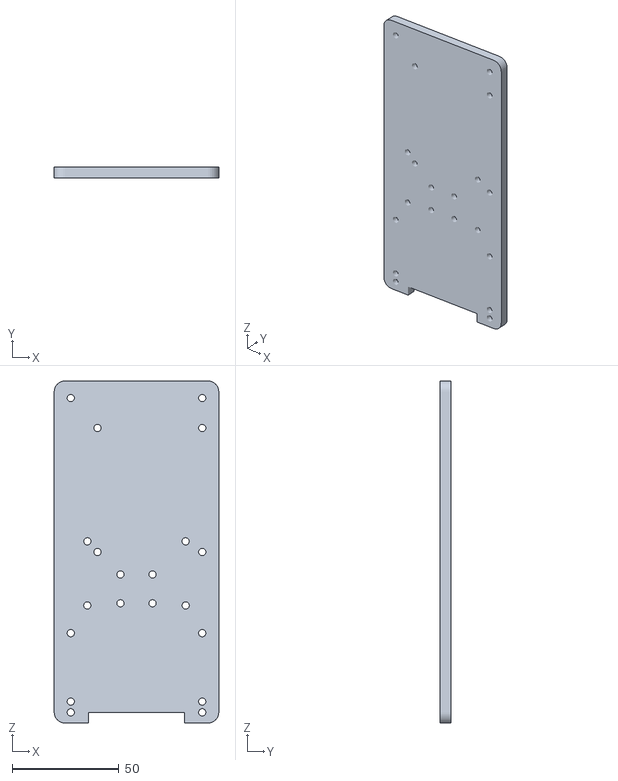
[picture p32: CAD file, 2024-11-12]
models/New robot (TR)/STL files/Top plate.stl
77.0 x 5.00 x 160.0

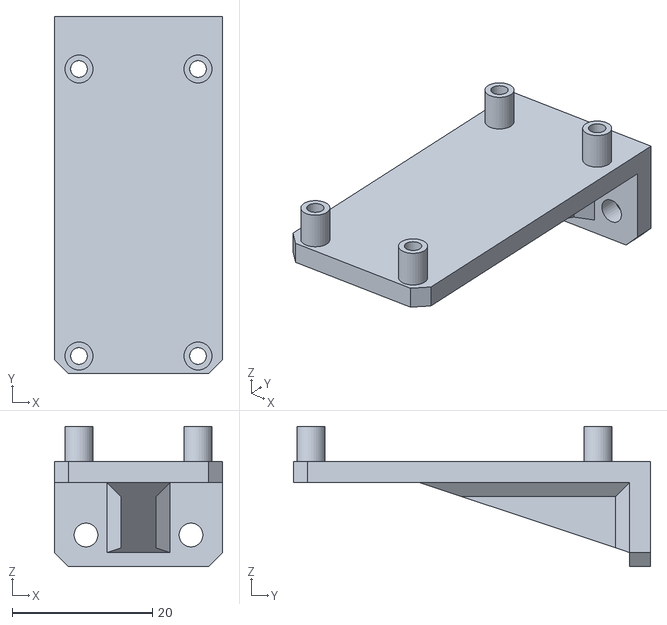
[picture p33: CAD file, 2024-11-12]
models/New robot (TR)/STL files/Vertical Ultrasonic Sensor Mount.stl
24.0 x 51.0 x 20.0

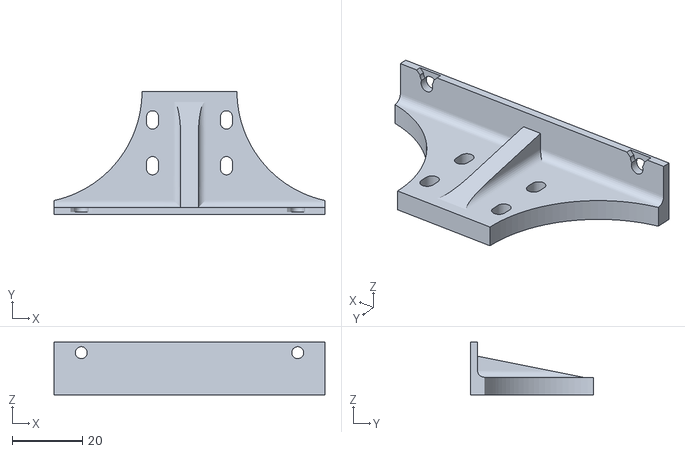
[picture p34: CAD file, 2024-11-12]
models/New robot (TR)/STL files/camera mount.stl
77.0 x 35.0 x 15.0

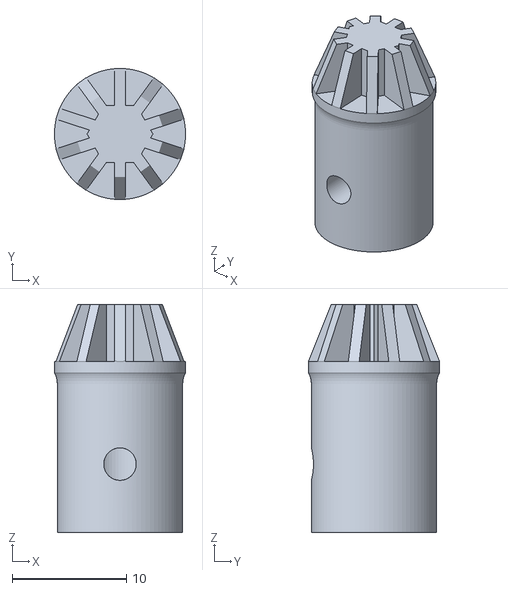
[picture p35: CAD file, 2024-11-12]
models/New robot (TR)/STL files/driver gear adapter v2.stl
11.5 x 11.5 x 20.0

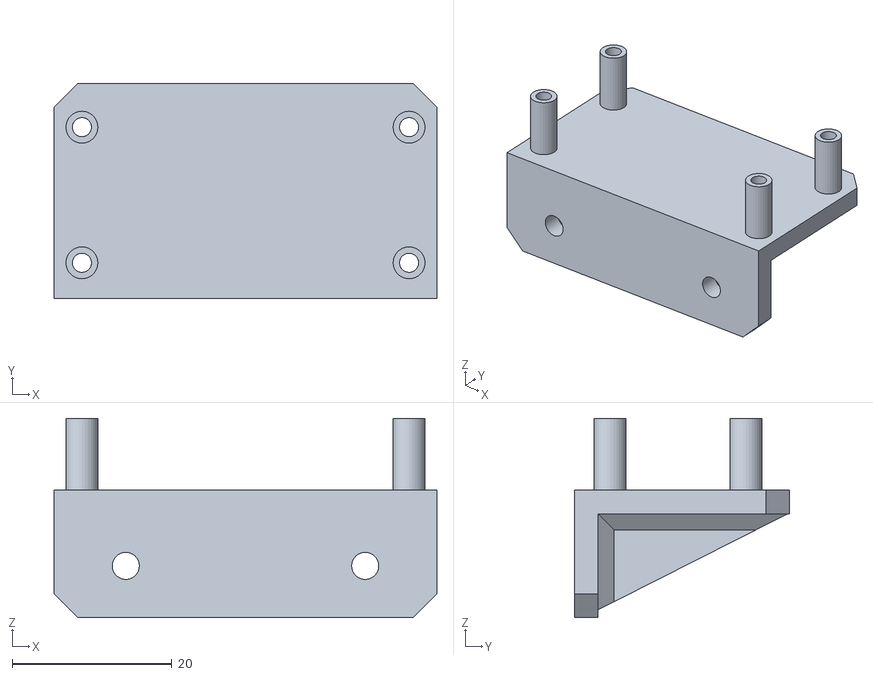
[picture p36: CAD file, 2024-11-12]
models/New robot (TR)/STL files/ultrasonic and headlight mount.stl
48.0 x 27.0 x 25.0

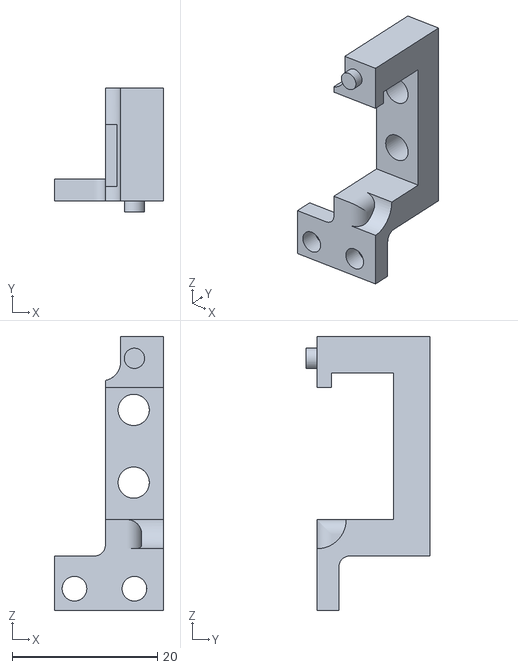
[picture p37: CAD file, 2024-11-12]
models/New robot (TR)/STL files/Servo mount.stl
15.0 x 17.0 x 37.7

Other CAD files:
models/Enginneering Drawings/top disassembly.dwg
models/Enginneering Drawings/bottom disassembly.dwg
models/vehicle 3D model/12v DC motor mount v2.stl
models/Enginneering Drawings/vehicle orthogonal drawing.dwg
models/Enginneering Drawings/vehicle isometric view.dwg
models/Disassembly Video/bottom disassembly.ipn
models/Disassembly Video/top disassembly.ipn
models/New robot (TR)/Autodesk Inventor/OldVersions/WRO FE vehicle v4.1.0074.iam
models/New robot (TR)/Autodesk Inventor/WRO FE vehicle v4.1.iam
models/New robot (TR)/Autodesk Inventor/vehicle v9/ActuatorLink.ipt
models/New robot (TR)/Autodesk Inventor/vehicle v9/Battery Mount V2.ipt
models/New robot (TR)/Autodesk Inventor/vehicle v9/Bottom plate.ipt
models/New robot (TR)/Autodesk Inventor/vehicle v9/DC+bearing mount.ipt
models/New robot (TR)/Autodesk Inventor/vehicle v9/IMU mount.ipt
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

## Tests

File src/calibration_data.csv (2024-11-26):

X | Y | Z
-62.437883659748614 | 37.06518561824028 | 13.402513884828998
-62.18941829874306 | 37.37211341712949 | 13.402513884828998
-62.18941829874306 | 37.37211341712949 | 13.402513884828998
-62.26249634609763 | 37.43057585501315 | 13.417129494299912
-62.26249634609763 | 37.43057585501315 | 13.417129494299912
-62.087109032446655 | 37.26980415083309 | 13.753288512130958
-62.087109032446655 | 37.26980415083309 | 13.753288512130958
-62.087109032446655 | 37.26980415083309 | 13.753288512130958
-62.45249926921953 | 37.67904121601871 | 12.890967553346973
-62.45249926921953 | 37.67904121601871 | 12.890967553346973
-62.554808535515924 | 37.54750073078048 | 12.730195849166911
-62.554808535515924 | 37.54750073078048 | 12.730195849166911
-62.335574393452205 | 37.562116340251386 | 12.96404560070155
-62.335574393452205 | 37.562116340251386 | 12.96404560070155
-62.335574393452205 | 37.562116340251386 | 12.96404560070155
-62.10172464191756 | 37.40134463607133 | 12.642502192341421
-62.10172464191756 | 37.40134463607133 | 12.642502192341421
-62.17480268927215 | 37.635194387605964 | 12.861736334405144
-62.17480268927215 | 37.635194387605964 | 12.861736334405144
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

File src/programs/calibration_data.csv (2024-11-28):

X | Y | Z
79 | -701 | 0
81 | -700 | -1
80 | -701 | 0
81 | -700 | -1
80 | -699 | -1
80 | -701 | 0
81 | -700 | 0
80 | -699 | -1
80 | -700 | 0
80 | -701 | 0
80 | -700 | 0
81 | -700 | 0
80 | -700 | -2
81 | -701 | 0
80 | -700 | 0
79 | -700 | 0
80 | -700 | 0
81 | -700 | 0
82 | -700 | -1
81 | -700 | 0
81 | -700 | 0
85 | -697 | 0
80 | -711 | 0
81 | -705 | 1
84 | -695 | -1
87 | -701 | 0
87 | -695 | -1
85 | -697 | -1
85 | -695 | -1
83 | -695 | -1
82 | -696 | 0
82 | -699 | 0
82 | -698 | -1
82 | -697 | 1
80 | -699 | 0
77 | -698 | -1
76 | -700 | -1
74 | -703 | 0
72 | -700 | 0
74 | -702 | 0
75 | -704 | 0
74 | -702 | -1
73 | -702 | -1
72 | -703 | -1
71 | -702 | 0
70 | -702 | -1
70 | -705 | -1
74 | -701 | -1
89 | -694 | -1
98 | -688 | 0
117 | -675 | 0
139 | -660 | 0
150 | -653 | 0
173 | -632 | 0
186 | -616 | -1
215 | -584 | -1
228 | -560 | -1
245 | -508 | 0
260 | -456 | 0
263 | -425 | 0
258 | -366 | 0
250 | -336 | -1
232 | -281 | 0
216 | -233 | 0
185 | -210 | 0
153 | -177 | -1
134 | -162 | -1
103 | -139 | -1
94 | -136 | -1
75 | -127 | 0
48 | -113 | -1
-7 | -100 | 0
-63 | -99 | 0
-94 | -103 | 0
-155 | -118 | -1
-180 | -130 | 0
-223 | -156 | 0
-245 | -173 | 1
-285 | -213 | 0
-312 | -259 | 0
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

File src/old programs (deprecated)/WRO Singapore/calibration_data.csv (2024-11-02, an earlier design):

X | Y | Z
412 | -262 | -1
410 | -267 | 0
407 | -277 | 0
386 | -348 | 0
366 | -393 | -1
310 | -477 | 0
263 | -529 | 1
239 | -547 | -1
168 | -596 | 0
130 | -618 | -1
53 | -641 | -1
11 | -652 | 0
-72 | -657 | 0
-156 | -649 | 0
-194 | -642 | -1
-270 | -612 | -1
-312 | -593 | -1
-388 | -543 | 0
-421 | -514 | 0
-479 | -447 | 0
-504 | -408 | -1
-543 | -327 | 0
-569 | -243 | 0
-575 | -195 | 0
-578 | -106 | 0
-571 | -56 | 0
-549 | 33 | -1
-532 | 73 | -1
-490 | 149 | 0
-433 | 219 | -1
-401 | 249 | -1
-334 | 299 | -1
-298 | 315 | -1
-217 | 347 | -1
-170 | 356 | 1
-79 | 363 | 1
14 | 353 | 0
59 | 342 | -2
146 | 306 | 0
183 | 287 | 0
255 | 230 | 0
285 | 201 | 0
342 | 125 | 0
366 | 43 | 255
399 | -1 | -1
419 | -91 | 0
422 | -139 | 0
418 | -228 | -1
410 | -273 | -1
385 | -350 | -1
369 | -388 | -1
326 | -463 | 0
269 | -523 | 0
237 | -553 | 0
165 | -600 | -1
128 | -619 | 0
50 | -645 | 0
12 | -650 | 0
-71 | -658 | -1
-157 | -651 | 0
-199 | -639 | -2
-283 | -610 | 0
-321 | -586 | 0
-397 | -536 | 0
-459 | -473 | 0
-486 | -435 | 0
-531 | -360 | -1
-546 | -316 | -1
-570 | -229 | 0
-576 | -183 | 0
-577 | -92 | -1
-560 | 1 | 0
-544 | 49 | -1
-506 | 125 | -1
-483 | 162 | 0
-427 | 226 | 0
-395 | 254 | -1
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

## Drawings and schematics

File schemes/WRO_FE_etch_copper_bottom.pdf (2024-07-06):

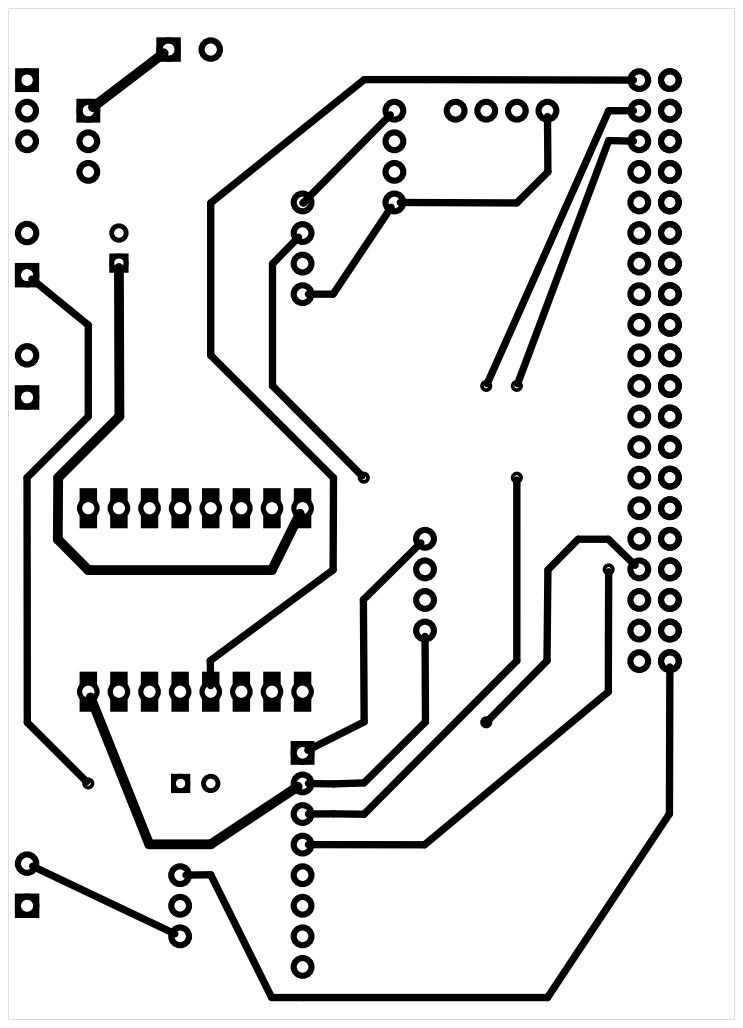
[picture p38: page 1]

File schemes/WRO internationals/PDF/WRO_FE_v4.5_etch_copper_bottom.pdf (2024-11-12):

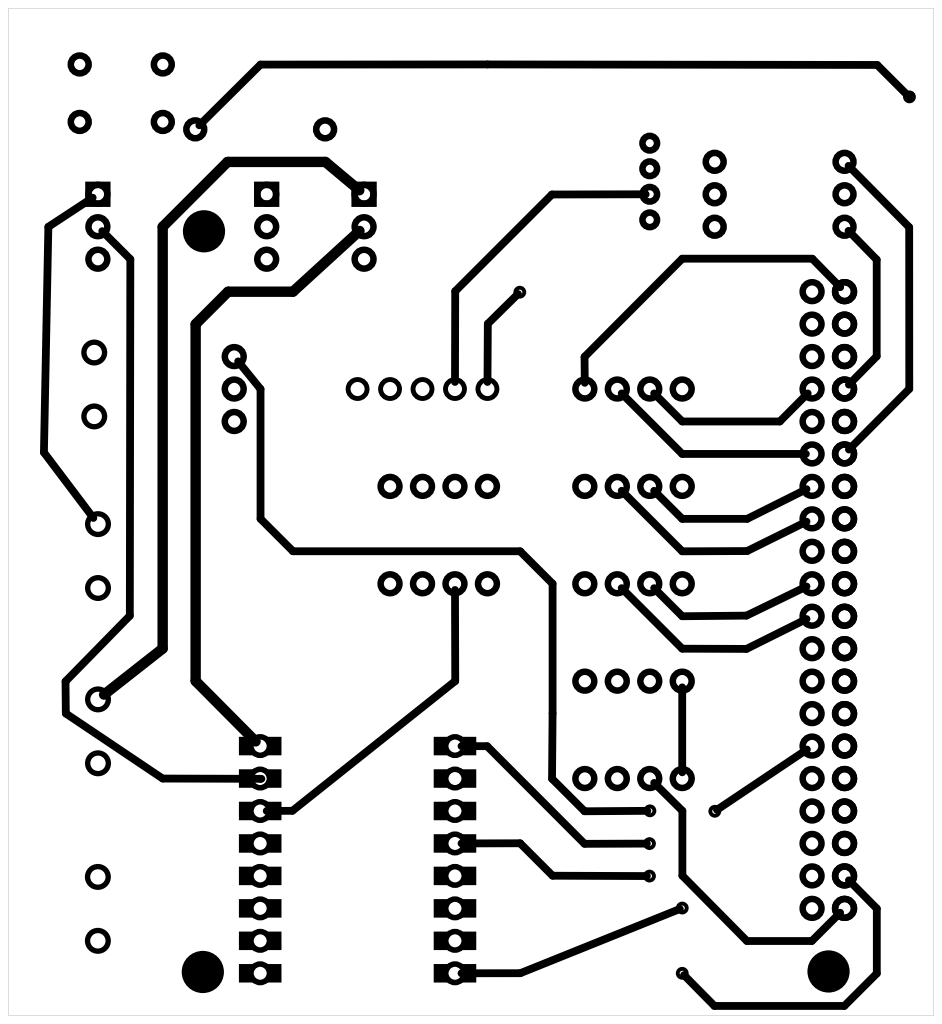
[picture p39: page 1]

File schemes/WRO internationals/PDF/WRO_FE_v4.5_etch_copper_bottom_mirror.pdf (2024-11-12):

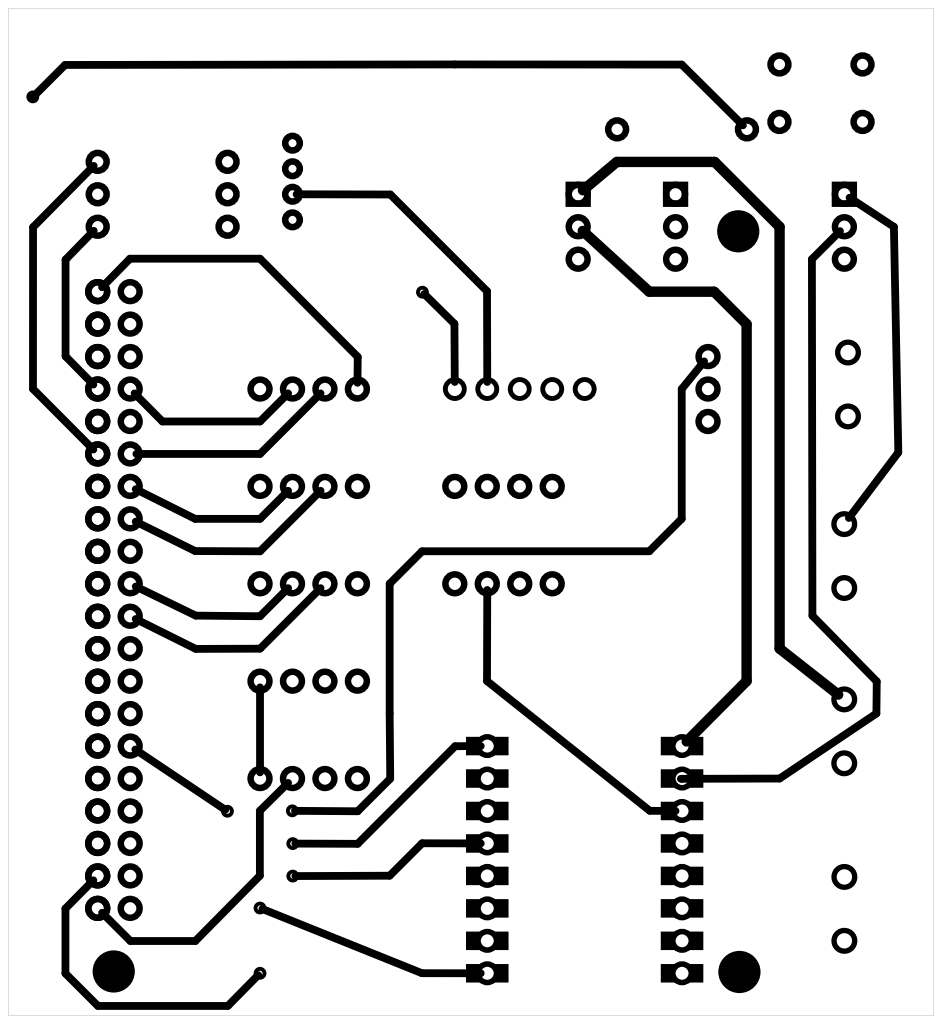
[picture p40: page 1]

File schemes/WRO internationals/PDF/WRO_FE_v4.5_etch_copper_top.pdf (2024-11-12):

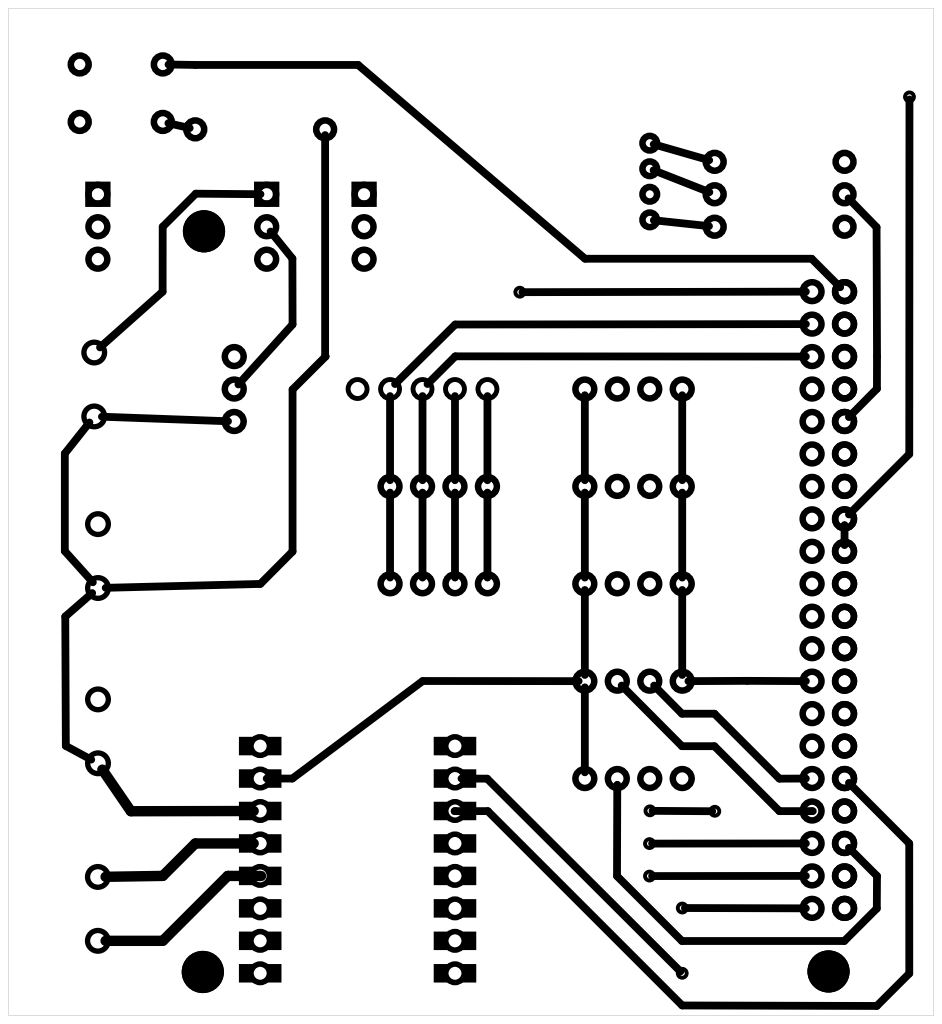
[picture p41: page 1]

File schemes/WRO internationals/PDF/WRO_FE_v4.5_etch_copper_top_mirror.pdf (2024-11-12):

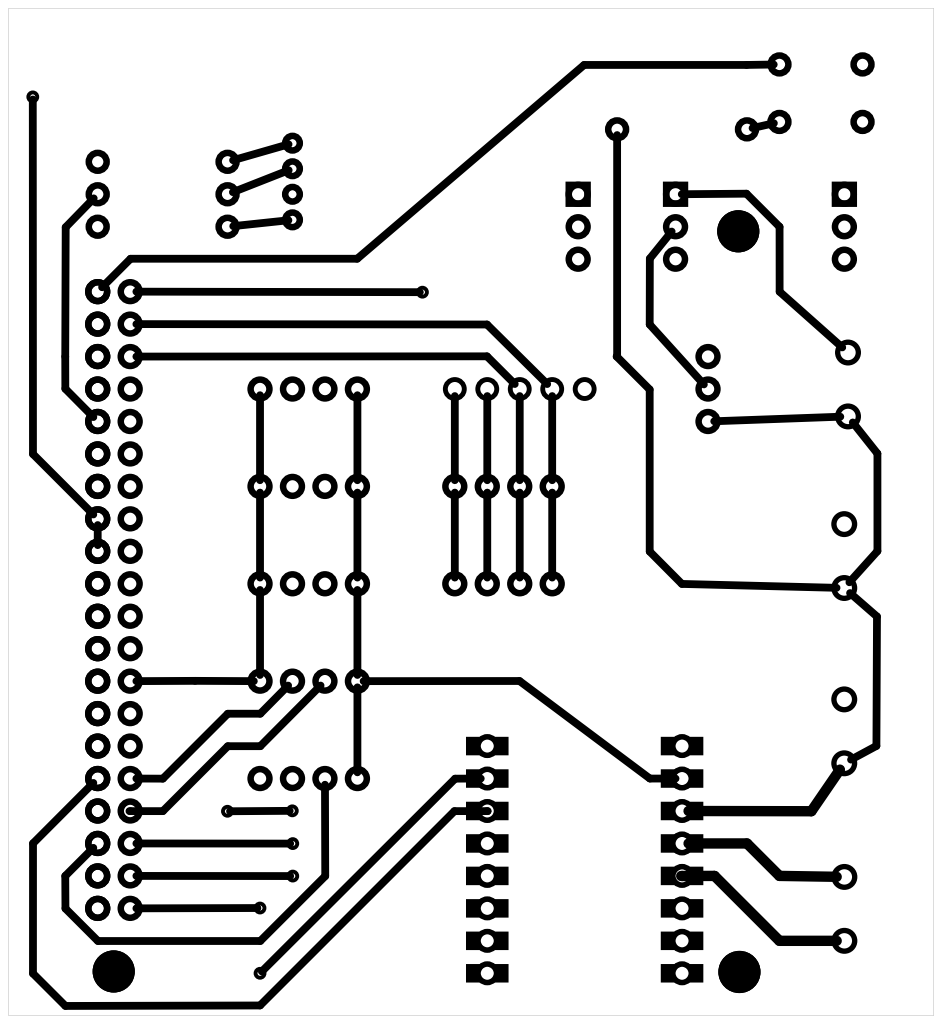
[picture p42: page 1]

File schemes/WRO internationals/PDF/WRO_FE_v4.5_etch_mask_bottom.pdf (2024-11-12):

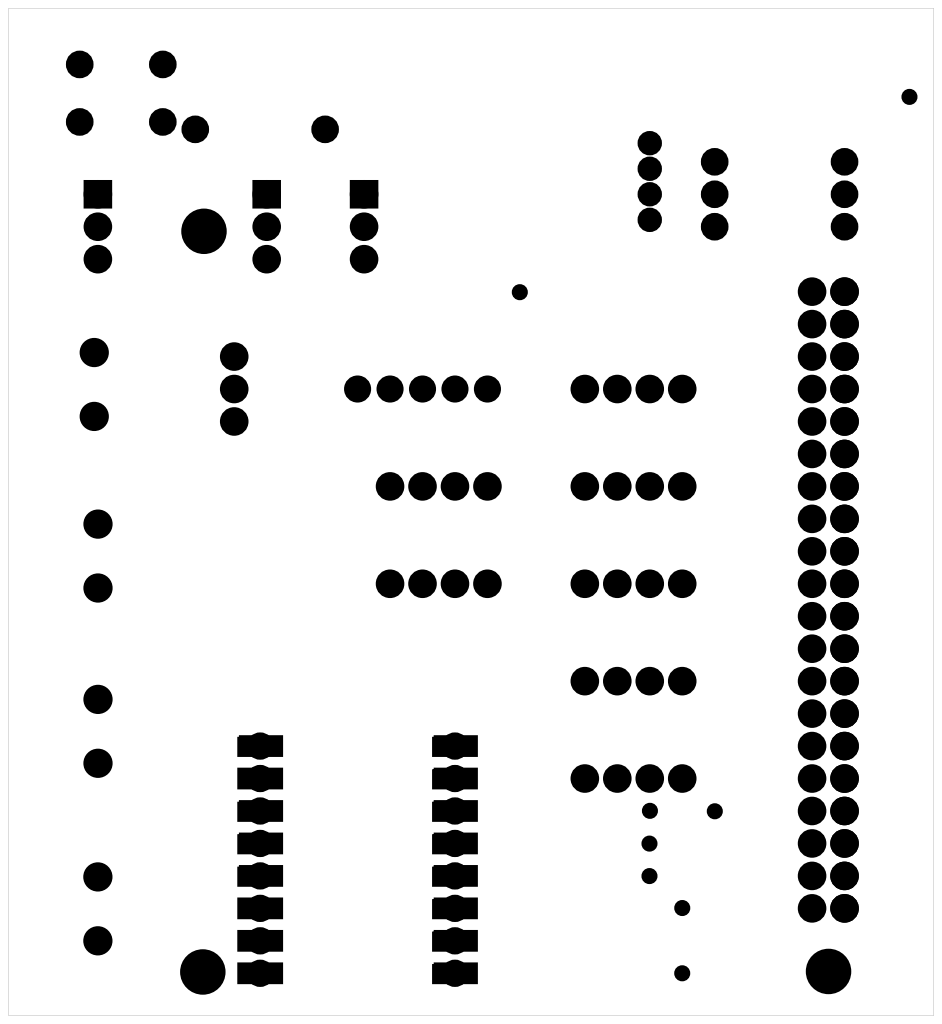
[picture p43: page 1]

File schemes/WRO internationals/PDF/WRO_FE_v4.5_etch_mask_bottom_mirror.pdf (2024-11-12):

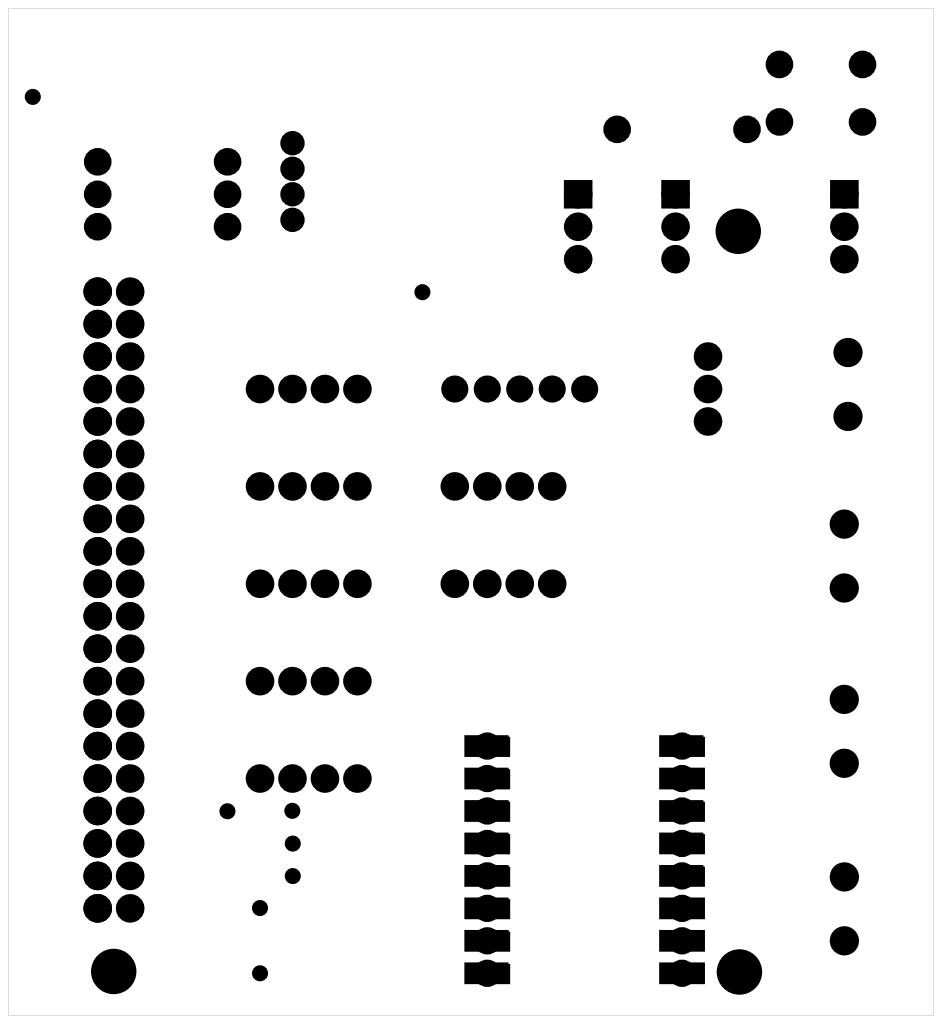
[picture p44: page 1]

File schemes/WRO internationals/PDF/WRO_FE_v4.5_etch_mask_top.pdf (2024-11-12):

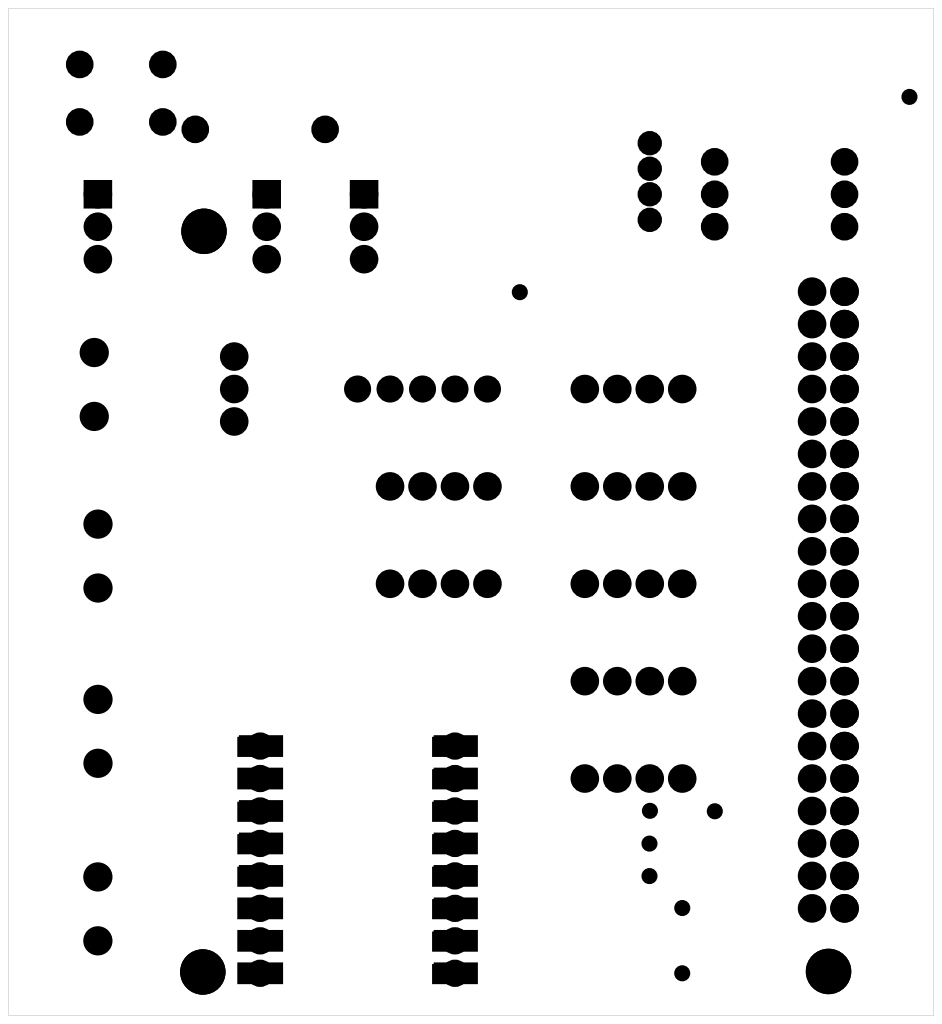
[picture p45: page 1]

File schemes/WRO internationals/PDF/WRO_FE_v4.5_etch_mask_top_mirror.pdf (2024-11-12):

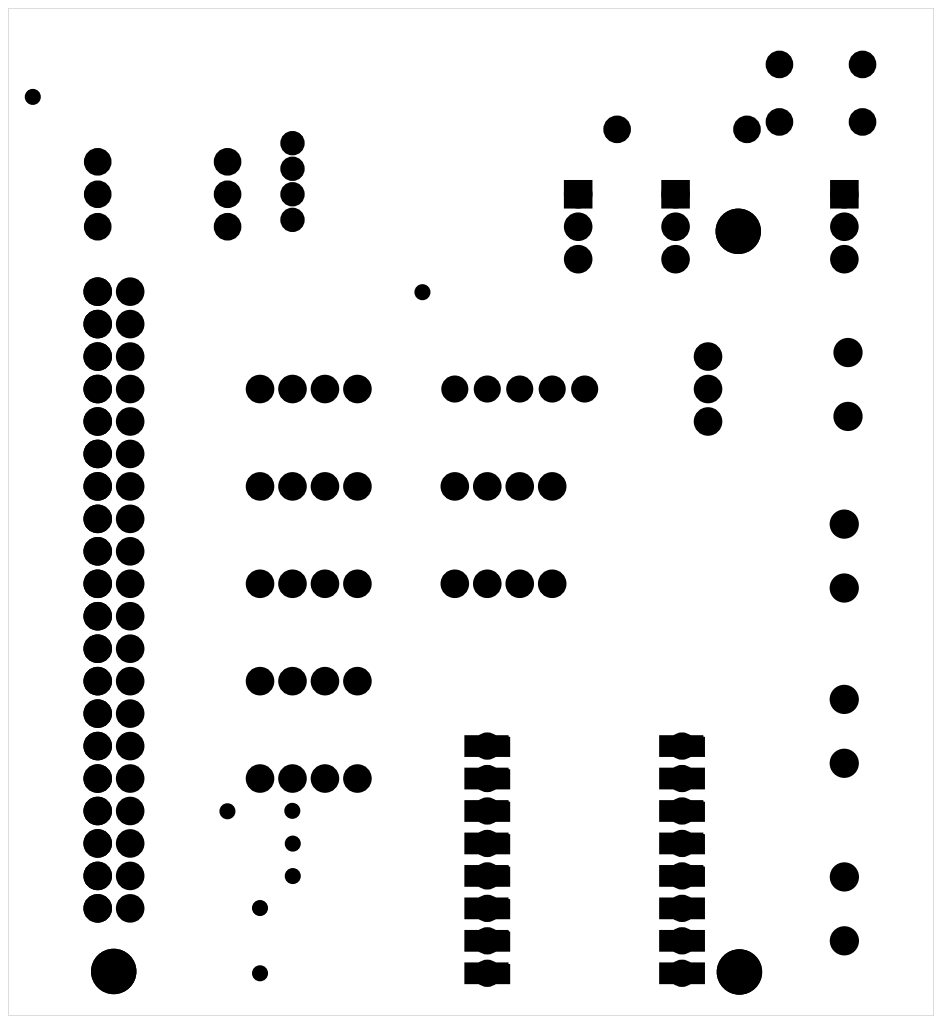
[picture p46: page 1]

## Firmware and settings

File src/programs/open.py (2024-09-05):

import RPi.GPIO as GPIO # use RPi library for controlling GPIO pins
import math
import time
from gpiozero.pins.pigpio import PiGPIOFactory
from collections import deque

# modules for controlling components
import modules.Tb6612fngControl as Tb6612fng
import modules.RGBLEDControl as RGB
import modules.HMC5883LControl as HMC5883L
import modules.ServoControl_gpiozero as myservo
from gpiozero import DistanceSensor

import cv2
from picamera2 import Picamera2
import numpy as np

GPIO.setwarnings(False) # turn off warnings for pins (if pins were previously used and not released properly there will be warnings)
GPIO.setmode(GPIO.BOARD) # pin name convention used is pin numbers on board
factory = PiGPIOFactory()

#variables
WHEELBASE = 12          # vehicle wheelbase in cm
TOTALROUNDS = 3         # total number of rounds to be completed  

drivingDirection = "CW"     # round driving direction
headingDirection = 0        # direction in which the robot should be heading in
noOfTurns = 0

compassDirection = 0  
leftDist = rightDist = frontDist = 0
actualLeft = actualRight = 0


# initialise components  
while True:
    try:
        compass = HMC5883L.compass(addr=0x1E)
    except OSError:
        print("Trying to connect to compass...")
        continue 
    print("Connection to compass successful!")
    break 

servo = myservo.myServo(gpioPin=5, startPos=0, offset=-5, minAng=-70, maxAng=70)
car = Tb6612fng.motor(stby=37, pwmA=35, ai1=36, ai2=40) 
LED = RGB.LED(red=8, blue=12, green=10)  

us2 = DistanceSensor(echo=27, trigger=22, max_distance=3, pin_factory=factory) # pins are gpio pins
# us3 = DistanceSensor(echo=10, trigger=9, max_distance=3, pin_factory=factory) # pins are gpio pins
us3 = DistanceSensor(echo=7, trigger=8, max_distance=3, pin_factory=factory) # pins are gpio pins
us4 = DistanceSensor(echo=6, trigger=13, max_distance=3, pin_factory=factory) # pins are gpio pins

# two pins are connected to the start button as safeguard
startBut1 = 16
startBut2 = 18
GPIO.setup(startBut1,GPIO.IN)
GPIO.setup(startBut2,GPIO.IN)

# camera vision 
# Define HSV color ranges for blue and orange
blue_lower, blue_upper = np.array([100, 20, 50]), np.array([150, 110, 90])
orange_lower, orange_upper = np.array([0, 145, 80]), np.array([10, 255, 150])

picam2 = Picamera2()
picam2.preview_configuration.main.size=(1920,1000)
picam2.preview_configuration.main.format = 'RGB888'
picam2.start()

def getAngularDiff(intendedAngle, currentAng): # cw => -ve ccw => +ve 

    angDiff = intendedAngle - currentAng

    if angDiff > 180:
        angDiff -= 360
    elif angDiff < -180:
        angDiff += 360
    return -angDiff

def turn(radius, direction, heading, tolerance = 10):  # turn radius in cm

    global compassDirection

    angleDiff = getAngularDiff(heading, compassDirection)

    if -tolerance <= angleDiff <= tolerance:
        return True
    else:
        if radius < WHEELBASE: # account for radius smaller than wheel base
            radius = WHEELBASE

        ang = math.degrees(math.asin(WHEELBASE/radius))

        if direction == "left":
            servo.write(ang)
        elif direction == "right":
            servo.write(-ang)

        return False

def keepStraight():

    global compassDirection, headingDirection

    error = getAngularDiff(headingDirection, compassDirection)

    Kp =  1
    P = error   

    return P*Kp

def keepInMiddle(leftDist, rightDist, setDist):

    global compassDirection, headingDirection

    ang = math.radians(getAngularDiff(compassDirection, headingDirection))
    error = round(leftDist*math.cos(ang) - rightDist*math.cos(ang)) + setDist

    Kp = 1

    P = error 

    return P*Kp 

def readSensors():

    global frontDist, leftDist, rightDist 
    global actualLeft, actualRight
    global compassDirection, headingDirection

    if headingDirection < 0:
        headingDirection += 360
    elif headingDirection > 360:
        headingDirection -= 360

    frontDist, leftDist, rightDist = round(us4.distance*100), round(us2.distance*100), round(us3.distance*100)
    
    ang = math.radians(getAngularDiff(compassDirection, headingDirection))
    actualLeft = abs(leftDist*math.cos(ang))
    actualRight = abs(rightDist*math.cos(ang))
    
    # read compass angle (catch exception when compass is not connected properly)
    while True:
        try:
            compassDirection = compass.getAngle()
        except OSError:
            print("trying to connect to compass")
            continue
        break

def getRoundDirection(hsv_frame, frame):
    BlueAngleSum = 0
    OranAngleSum = 0
    BlueMean = 0
    OranMean = 0
    for d in range(0,5):
        # Create masks for blue and orange
        blue_mask = cv2.inRange(hsv_frame, blue_lower, blue_upper)
        orange_mask = cv2.inRange(hsv_frame, orange_lower, orange_upper)
        # Use Hough Line Transform to detect lines
        lineB = cv2.HoughLinesP(blue_mask, 1, np.pi / 180, threshold=100, minLineLength=100, maxLineGap=5)
        lineO = cv2.HoughLinesP(orange_mask, 1, np.pi / 180, threshold=100, minLineLength=100, maxLineGap=5)
        
        # Check if any lines were found
        if lineB is not None:
            for line in lineB:
                xB1, yB1, xB2, yB2 = line[0]
        
            # Calculate the angle of the line
            angleB = abs(np.degrees(np.arctan2(yB2 - yB1, xB2 - xB1)))
            BlueAngleSum += angleB
            print(f" Blue Line from ({xB1}, {yB1}) to ({xB2}, {yB2}) has an angle of {angleB:.2f} degrees")
    
            # Draw the line on the image
            cv2.line(frame, (xB1, yB1), (xB2, yB2), (0, 255, 0), 2)
        if lineO is not None:
            for line in lineO:
                xO1, yO1, xO2, yO2 = line[0]
        
            # Calculate the angle of the line
            angleO = abs(np.degrees(np.arctan2(yO2 - yO1, xO2 - xO1)))
            OranAngleSum += angleO
            print(f"Orange Line from ({xO1}, {yO1}) to ({xO2}, {yO2}) has an angle of {angleO:.2f} degrees")
    
            # Draw the line on the image
            cv2.line(frame, (xO1, yO1), (xO2, yO2), (0, 255, 0), 2)
        else:
            return "unknown"
    BlueMean = abs(BlueAngleSum)/5
    OranMean = abs(OranAngleSum)/5
    if BlueMean > OranMean:
        LED.rgb(255,165,0)
        return "CW"
    if OranMean > BlueMean:
        LED.rgb(0,0,225)
        return "ACW"
    else:   
        print("No blue or orange detected in the frame")
        return "unknown"
    

def executeAction(action):

    global headingDirection, drivingDirection
    TurnHeadingDirection = 0

    completed = None

    match action[0].split()[0]:

        case "corner_turn":
            LED.rgb(0,0,255) # blue light

            direction = "right" if drivingDirection == "CW" else "left"
            if drivingDirection == "CW":
                TurnHeadingDirection = headingDirection - 10
            else:
                TurnHeadingDirection = headingDirection + 10
            completed = turn(20, direction, TurnHeadingDirection, tolerance=10)

            car.speed(40)

        case "avoid_right":
    
            LED.rgb(255,0,255) # purple light

            completed = turn(20, "right", heading=int(action[0].split()[1]), tolerance=10)

            car.speed(30)

        case "recover_left":

            LED.rgb(255,255,0) # yellow light

            completed = turn(25, "left", heading=headingDirection+5, tolerance=5)
            car.speed(30)
            
        case "avoid_left":
    
            LED.rgb(255,0,255) # purple light

            completed = turn(20, "left", heading=int(action[0].split()[1]), tolerance=10)

            car.speed(30)

        case "recover_right":

            LED.rgb(255,255,0) # yellow light

            completed = turn(25, "right", heading=headingDirection-5, tolerance=5)
            car.speed(30)
            
        case "run":
            LED.rgb(0,255,0) # green light
            car.speed(770)
            servoAng = keepStraight()
            servo.write(servoAng)
            completed = True

    if completed == True:
        action.popleft()
            

def main():

    actionQueue = deque()   
    start = False
    canTurn = False

    startFront = 0

    global frontDist, leftDist, rightDist 
    global actualLeft, actualRight
    global headingDirection, compassDirection, noOfTurns, drivingDirection

    while True:

        frame = picam2.capture_array()
        frame = cv2.flip(frame, 0) # Flip vertically
        frame = cv2.flip(frame, 1) # Flip horizontally

        # Convert the frame to HSV color space
        hsv_frame = cv2.cvtColor(frame, cv2.COLOR_BGR2HSV)

        blue_mask = cv2.inRange(hsv_frame, blue_lower, blue_upper)
        orange_mask = cv2.inRange(hsv_frame, orange_lower, orange_upper)

        #cv2.imshow('preview', frame)

        readSensors()

        print(f"compassDirec: {compassDirection}, heading: {headingDirection} drivingDirection: {drivingDirection} f: {frontDist}, l: {leftDist} r: {rightDist}")

        # start the robot when button pressed
        if GPIO.input(startBut1) and GPIO.input(startBut2):
            start = True

            # reset variabls
            headingDirection = noOfTurns = 0
            startFront = frontDist
            canTurn = True
            actionQueue.clear()
            compass.setHome()

            readSensors()   

            drivingDirection = getRoundDirection(hsv_frame, frame)
            time.sleep(0.5)

        
        # stop the robot when 3 rounds completed
        if noOfTurns == 4 * TOTALROUNDS and startFront - 15 <= frontDist <= startFront + 8 and canTurn == True:
            start = False

        if start:

            if actionQueue:
                pass
            elif frontDist <= 80 and canTurn: #

                canTurn = False

                if noOfTurns == 0 and drivingDirection == "unknown":
                    if leftDist <= rightDist:
                        drivingDirection = "CW"
                    elif leftDist > rightDist:
                        drivingDirection = "ACW"

                headingDirection += 90 if drivingDirection == "CW" else -90 

                noOfTurns += 1

                actionQueue = deque(["corner_turn", "run"])

            elif leftDist <= 15:

                actionQueue = deque([f"avoid_right {headingDirection+30}", "recover_left"])

            elif rightDist <= 15:

                actionQueue = deque([f"avoid_left {headingDirection-30}", "recover_right"])

            else:
                actionQueue = deque(["run"])

            if frontDist >= 130:
                canTurn = True
            

            executeAction(actionQueue)
            
        else:
            car.speed(0)
            servo.write(0)
            LED.off()

        if cv2.waitKey(1) == ord('q'):
            break

if __name__ == "__main__":
    try:
        main()
    except KeyboardInterrupt:
        picam2.stop()
        cv2.destroyAllWindows() 
        GPIO.cleanup()




# import RPi.GPIO as GPIO # use RPi library for controlling GPIO pins
# import time
# import math
# from gpiozero.pins.pigpio import PiGPIOFactory

# # modules for controlling components
# import modules.Tb6612fngControl as Tb6612fng
# import modules.RGBLEDControl as RGB
# import modules.HMC5883LControl as HMC5883L
# import modules.ServoControl_gpiozero as myservo
# from gpiozero import DistanceSensor

# GPIO.setwarnings(False) # turn off warnings for pins (if pins were previously used and not released properly there will be warnings)
# GPIO.setmode(GPIO.BOARD) # pin name convention used is pin numbers on board
# factory = PiGPIOFactory()

# #variables
# WHEELBASE = 12          # vehicle wheelbase in cm
# TOTALROUNDS = 3
# compassDirection = 0    # headings from the compass module
# drivingDirection = "CW" # round driving direction

# # initialise components  
# try: 
#     compass = HMC5883L.compass(addr=0x1E)
# except OSError:

#     while True:

#         print("Trying to connect to compass...")
#         try:
#             compass = HMC5883L.compass(addr=0x1E)
#         except OSError:
#             continue 
#         print("Connection successful!")
#         break 

# servo = myservo.myServo(gpioPin=5, startPos=0, offset=-13, minAng=-70, maxAng=70)
# car = Tb6612fng.motor(stby=37, pwmA=35, ai1=36, ai2=40) 
# LED = RGB.LED(red=8, blue=12, green=10)  

# us2 = DistanceSensor(echo=27, trigger=22, max_distance=3, pin_factory=factory) # pins are gpio pins
# us3 = DistanceSensor(echo=10, trigger=9, max_distance=3, pin_factory=factory) # pins are gpio pins
# us4 = DistanceSensor(echo=6, trigger=13, max_distance=3, pin_factory=factory) # pins are gpio pins

# startBut1 = 16
# startBut2 = 18
# GPIO.setup(startBut1,GPIO.IN)
# GPIO.setup(startBut2,GPIO.IN)

# def getAngularDiff(intendedAngle, currentAng): # cw => -ve ccw => +ve 

#     angDiff = intendedAngle - currentAng

#     if angDiff > 180:
#         angDiff -= 360
#     elif angDiff < -180:
#         angDiff += 360
#     return -angDiff

# # radius is in cm
# def turn(radius, headingDirection, direction, curAct, nextAct): 

#     angTolerance = 7

#     angleDiff = getAngularDiff(headingDirection, compassDirection)

#     if -angTolerance <= angleDiff <= angTolerance:
#         return nextAct
#     else:
#         if radius < WHEELBASE:
#             radius = WHEELBASE

#         ang = math.degrees(math.asin(WHEELBASE/radius))
#         if direction == "left":
#             servo.write(ang)
#             return curAct
#         elif direction == "right":
#             servo.write(-ang)
#             return curAct

# def keepStraight(headingDirection):

#     global compassDirection

#     error = getAngularDiff(headingDirection, compassDirection)

#     Kp =  0.5
#     P = error   

#     return P*Kp

# def keepInMiddle(headingDirection, leftDist, rightDist, setDist):

#     global compassDirection

#     ang = math.radians(getAngularDiff(compassDirection, headingDirection))
#     error = round(leftDist*math.cos(ang) - rightDist*math.cos(ang)) + setDist

#     Kp = 1

#     P = error 

#     return P*Kp 

# def main():

#     global drivingDirection
#     global compassDirection
#     global TOTALROUNDS

#     action = None
#     canTurn = True
#     start = False
#     noOfTurns = 0
#     headingDirection = 0
#     ignore = False
#     turnDist = 0

#     initialFront = initialLeft = initialRight = None

#     while True:

#         if headingDirection < 0:
#             headingDirection += 360
#         elif headingDirection > 360:
#             headingDirection -= 360

#         # get US distances in cm
#         frontDist, leftDist, rightDist = round(us4.distance*100), round(us2.distance*100), round(us3.distance*100)

#         #print(f"Front: {frontDist} But1: {GPIO.input(startBut1)}  But2: {GPIO.input(startBut2)} compass: {compassDirection} headingDirection: {headingDirection}")
#         if GPIO.input(startBut1) and GPIO.input(startBut2): # start the program
#             start = True

#             # reset variables
#             headingDirection = 0
#             canTurn = True
#             noOfTurns = 0
#             action = None
#             ignore = False

#             initialFront = frontDist
#             initialLeft = leftDist
#             initialRight = rightDist

#             LED.rgb(255,255,255)
#             time.sleep(0.5)
        
#             compass.calibrate(True) # set direction value to 0 when button pressed
#             doOnce = 0

#         if start:

#             # get compass direction
#             try:
#                 compassDirection = compass.getAngle()
#             except OSError:
#                 while True:
#                     print("Trying to connect to compass...")
#                     try:
#                         compassDirection = compass.getAngle()
#                     except OSError:
#                         continue 
#                     print("Connection successful!")
#                     break 

#             ang = math.radians(getAngularDiff(compassDirection, headingDirection))
#             actualLeft = abs(leftDist*math.cos(ang))
#             actualRight = abs(rightDist*math.cos(ang))

#             #print(f"actualLeft: {actualLeft}, compassDirection: {compassDirection}, headingDirection: {headingDirection}")
        
#             if frontDist <= 70 and canTurn:

#                 canTurn = False

#                 if noOfTurns == 0: # determine driving direction
#                     if leftDist <= rightDist:
#                         drivingDirection = "CW"
#                     elif leftDist > rightDist: 
#                         drivingDirection = "ACW"
                
#                 if drivingDirection == "CW":
#                     action = "corner right"
#                     headingDirection += 90
#                 else:
#                     action = "corner left"
#                     headingDirection -= 90

#                 noOfTurns += 1
#             # elif 0<= actualLeft <= 20 and leftDist <= 60 and frontDist >= 100:
#             #     print("turning back")
#             #     direc = headingDirection + 45
#             #     action = "avoid right"
#             #     ignore = True
#             #     turnDist = actualLeft
#             # elif 0<= actualRight <= 20 and rightDist <= 60 and frontDist >= 50 and action != "corner right" and action != "corner left":
#             #     print("turning back")
#             #     direc = headingDirection - 45
#             #     action = "avoid left"
#             #     ignore = True
#             #     turnDist = actualRight

#             if frontDist >= 130: # reset variable
#                 canTurn = True

#             if noOfTurns == 4*TOTALROUNDS and initialFront-10 <= frontDist <= initialFront+8: # stop when finished
#                 start = False

#             print(f"heading: {compass.heading} startPos: {compass.startPos} compass: {compassDirection} actualRight: {round(actualRight)} headingDirection: {headingDirection} front: {frontDist} left: {leftDist} right: {rightDist} angle:  noOfTurns: {noOfTurns} actualLeft: {actualLeft} action: {action}")

#             match action:

#                 case "corner right":
#                     action = turn(20, headingDirection, "right", curAct=action, nextAct=None)
#                     LED.rgb(0, 0, 255) # LED blue

#                 case "corner left":
#                     action = turn(20, headingDirection, "left", curAct=action, nextAct=None)
#                     LED.rgb(0, 0, 255) # LED blue

#                 case "avoid right":
#                     action = turn(15, direc, "right", curAct=action, nextAct="recover left")
#                     LED.rgb(255, 0, 255) # LED purple 
#                     car.speed(20)

#                     action = turn(15, headingDirection, "left", curAct=action, nextAct=None)
#                     action = turn(15, headingDirection, "left", curAct=action, nextAct=None)
#                     LED.rgb(255, 180, 155) # LED purple 
#                     car.speed(15)

#                     if action == None:
#                         ignore = False

#                 case "avoid left":
#                     action = turn(15, direc, "left", curAct=action, nextAct="recover right")
#                     LED.rgb(255, 0, 255) # LED purple 
#                     car.speed(20)

#                 case "recover right":
#                     action = turn(15, headingDirection, "right", curAct=action, nextAct=None)
#                     LED.rgb(255, 180, 155) # LED white
#                     car.speed(15)

#                     if action == None:
#                         ignore = False

#                 case _:  

#                     LED.rgb(0,255,0)
#                     angle = keepStraight(headingDirection)
#                     servo.write(angle)
#                     car.speed(40)
#         else:
#             # reset vehicle components
#             servo.write(0)
#             car.speed(0)
#             LED.off()

# if __name__ == "__main__":
#     try:
#         main()
#     except KeyboardInterrupt:
#         GPIO.cleanup()

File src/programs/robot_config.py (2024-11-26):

"""
This file stores the pin connections and component configurations for the robot.
May consider using a yaml file instead.
"""

# Datasheets:
# Pi Cam: https://www.raspberrypi.com/documentation/accessories/camera.html
# US-015: https://downloads.autobotic.com.my/3822/3822%20US-015%20High%20Accuracy%20Ultrasonic%20Sensor.pdf
# TB6612FNG: https://www.sparkfun.com/datasheets/Robotics/TB6612FNG.pdf 


# old robot configuration
# ------------------------------------------------------------------------------------------

# camera={"shape": (640,480), "vertical FOV": 41, "horizontal FOV": 66, "focal length": 390}

# # gpio pin convention
# servo={"pin":5,"start":0, "offset":-5, "min":-60, "max":60}  # pin 29 (physical)
# us1={"trig":17, "echo":4} # 11, 7 (physical)
# us2={"trig":22, "echo":27} # 15, 13 (physical)
# us3={"trig":9, "echo":10} # 21, 19 (physical)
# us4={"trig":13, "echo":6} # 33, 31 (physical)
# us5={"trig":8, "echo":7}  # 36, 40 (physical)
# rgb={"red":14, "green":15, "blue":18}  # 8, 10, 12 (physical) 
# pb={1: 23, 2: 24} # 16, 18 (physical)
# mDrvr={"stby": 26, "pwmA": 19, "ai1": 16, "ai2": 21} # 37, 35, 36, 40  (physical)

# MAX_SPEED_CMS = 44 #cm/s
# CAR_WIDTH = 17 # cm
# CAR_LENGTH = 18.5 # cm
# WHEELBASE = 12 # cm

# new robot configuration 
# -------------------------------------------------------------------------------------------

camera={"shape": (640,480), "vertical FOV": 67, "horizontal FOV": 102, "focal length": 390}

# gpio pin convention
servo={"pin":5,"start":0, "offset":-6, "min":-50, "max":50} # pin 29 (physical)
us_front={"trig":17, "echo":4} # 11, 7 (physical)
us_left={"trig":22, "echo":27} # 15, 13 (physical)
us_right={"trig":9, "echo":10} # 21, 19 (physical)
us_spare1={"trig":13, "echo":6} # 33, 31 (physical)
us_spare2={"trig":16, "echo":21} # 36, 40 (physical)
rgb={"red":14, "green":18, "blue":15} # 8, 12, 10 (physical)
pb={1: 23, 2: 24} # 16, 18 (physical)
mDrvr={"stby":26, "pwmA":19, "ai1":12, "ai2":20} # 37, 35, 32, 38  (physical)
tof_left = {"x shut":11} # 23 (physical)
tof_right = {"x shut":8} # 24 (physical)
tof_back = {"x shut":25} # 22 (physical)

MAX_SPEED_CMS = 35 #cm/s
CAR_WIDTH = 13.5 # cm
CAR_LENGTH = 17.5 # cm
CAR_HEIGHT = 30 # cm
WHEELBASE = 11 # cm

FRONT_2_TOF_LEN =10 # cm

# coordinates of servo axis w.r.t top left pivot as origin 
SERVO_CTR = (2.7, 1.05) #(3,1.5) # cm
# yoke length
YOKE = 5 # cm
# steering link length
ANGLED_LINK = 2.5 # cm
DIST_BTW_PIVOTS = 6 # cm
ANGLED_LINK_ANG_OFFSET = 78.5 # degrees

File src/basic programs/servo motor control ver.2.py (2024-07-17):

import RPi.GPIO as GPIO
import time
import ultrasonicSensor_control as us

# Initialize GPIO
GPIO.setwarnings(False)
GPIO.setmode(GPIO.BOARD)

# Define pin numbers
pwmA = 11   # Motor PWM
ai2 = 13    # Motor Input 2
ai1 = 15    # Motor Input 1
servo = 19  # Servo PWM

# Ultrasonic sensor pins
front_trigger_pin = 16
front_echo_pin = 18
left_trigger_pin = 22
left_echo_pin = 21
right_trigger_pin = 24
right_echo_pin = 23

# Set up motor driver pins
GPIO.setup(pwmA, GPIO.OUT)
GPIO.setup(ai2, GPIO.OUT)
GPIO.setup(ai1, GPIO.OUT)

# Set up servo motor
GPIO.setup(servo, GPIO.OUT)
servo_pwm = GPIO.PWM(servo, 50)  # PWM frequency for servo (50 Hz)
servo_pwm.start(5)  # Initial position of servo

# Set up PWM for motor speed control
pi_pwm = GPIO.PWM(pwmA, 100)  # PWM frequency for motor (100 Hz)
pi_pwm.start(0)  # Initial duty cycle (0%)

# Set up ultrasonic sensors
front_sensor = us.ultrasonic(front_trigger_pin, front_echo_pin)
left_sensor = us.ultrasonic(left_trigger_pin, left_echo_pin)
right_sensor = us.ultrasonic(right_trigger_pin, right_echo_pin)

# Function to control servo angle
def set_servo_angle(angle):
    # Map angle (0 to 180 degrees) to PWM duty cycle (2.5 to 12.5)
    duty = angle / 18.0 + 2.5
    servo_pwm.ChangeDutyCycle(duty)

# Main control loop
while True:
    # Read distances from sensors
    front_distance = front_sensor.getDist()
    left_distance = left_sensor.getDist()
    right_distance = right_sensor.getDist()

    print(f"Front Distance: {front_distance} cm, Left Distance: {left_distance} cm, Right Distance: {right_distance} cm")

    userInput = input()

    if userInput.startswith(('f', 'b', 'r', 'l', 'u', 's')):
        direction = userInput[0]
        speed = userInput[1:]

        try:
            pi_pwm.ChangeDutyCycle(int(speed))
        except ValueError:
            speed = 0

        if direction == 'f':  # forward
            GPIO.output(ai1, GPIO.HIGH)
            GPIO.output(ai2, GPIO.LOW)

        elif direction == 'b':  # backward
            GPIO.output(ai1, GPIO.LOW)
            GPIO.output(ai2, GPIO.HIGH)

        elif direction == 'r':  # right
            set_servo_angle(90)  # Adjust angle as needed for right turn

        elif direction == 'l':  # left
            set_servo_angle(0)  # Adjust angle as needed for left turn

        elif direction == 'u':  # up or center position
            set_servo_angle(45)  # Adjust angle as needed for center position

        elif direction == 's':  # stop
            GPIO.output(ai1, GPIO.LOW)
            GPIO.output(ai2, GPIO.LOW)

    # Steering using sensor readings
    # If front sensor detects an obstacle and both left and right distances are valid
    if front_distance < 20 and left_distance > 0 and right_distance > 0:
        if left_distance > right_distance:
            set_servo_angle(0)  # Steer left
        else:
            set_servo_angle(90)  # Steer right

    elif userInput == 'e':  # exit program
        GPIO.cleanup()  # Release GPIO pins
        break

    time.sleep(0.1)  # Add a small delay to control loop for stability

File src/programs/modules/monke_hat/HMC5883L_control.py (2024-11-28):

"""
Changing i2c frequency for RPI:
- Add this to/boot/firmware/config.txt, "dtparam=i2c_arm=on,i2c_arm_baudrate=400000"
- Reboot pi
"""

import smbus
import math

class Compass:
    """
    Class for utilising the HMC5883L magnetometer module

    Methods
    -------
    read_raw_data(addr)
    compute_heading(x,y)
    get_angle(relative=True)
    apply_calibration(raw_x, raw_y, raw_z)
    set_home(signal=True)
    """

    # HMC5883L register addresses
    CONFIG_A = 0x00
    CONFIG_B = 0x01
    MODE = 0x02
    X_MSB = 0x03
    Z_MSB = 0x05
    Y_MSB = 0x07

    # area specific alterations
    DECLINATION_ANGLE = 0.22
    # X_OFFSET, Y_OFFSET, Z_OFFSET = -28.0, -138.0, 0
    # X_SCALE, Y_SCALE, Z_SCALE = 511.0, 498.0, 1
    X_OFFSET, Y_OFFSET, Z_OFFSET = -45.0, -414.5, 0
    X_SCALE, Y_SCALE, Z_SCALE = 332.0, 345.5, 2
    bus = None

    def __init__(self, addr=0x1E):
        """
        Parameters
        ----------

        addr: int
            i2c Address of HMC5583L module. (Default is 0x1E) 
            Fake China clones have a different address. 
        """

        self.bus = smbus.SMBus(1)

        self.ADDRESS = addr

        self.bus.write_byte_data(self.ADDRESS, self.CONFIG_A, 0x70)  # Set to 8 samples @ 15Hz
        self.bus.write_byte_data(self.ADDRESS, self.CONFIG_B, 0x20)  # 1.3 gain LSb / Gauss 1090 (default)
        self.bus.write_byte_data(self.ADDRESS, self.MODE, 0x00)  # Continuous measurement mode

        self.startPos = 0

    def read_raw_data(self, addr) -> int:
        """
        Reads 16 bit value from HMC5583L registers

        Parameters
        ----------

        addr: int
            HMC5883L register addresses
        """

        high = self.bus.read_byte_data(self.ADDRESS, addr)
        low = self.bus.read_byte_data(self.ADDRESS, addr+1)
        
        # Combine them to get a 16-bit value
        value = (high << 8) + low
        if value > 32768:  # Adjust for 2's complement
            value = value - 65536
        return value
    
    def compute_heading(self, x, y):
        """
        Calculate heading in radians

        Parameters
        ----------
        x: int
            16 bit value from x register
        y: int
            16 bit value from y register
        """

        heading_rad = math.atan2(y, x)
        
        heading_rad += self.DECLINATION_ANGLE  # Adjust for declination angle (e.g. 0.22 for ~13 degrees)
        
        # Correct for when signs are reversed.
        if heading_rad < 0:
            heading_rad += 2 * math.pi
    
        # Check for wrap due to addition of declination.
        if heading_rad > 2 * math.pi:
            heading_rad -= 2 * math.pi

        return math.degrees(heading_rad)

    def get_angle(self, relative=True) -> int:
        """
        Get heading from HMC5883L compass. 0-360 degrees

        Read the raw values from each axes, apply offset values and calculate heading.
        Parameters
        ----------
        relative: bool
            True: Return the heading of the compass relative to the home position.
            False: Return the true heading
        """
        # read compass angle (catch exception when compass is not connected properly)
        x = self.read_raw_data(self.X_MSB)
        y = self.read_raw_data(self.Y_MSB)
        z = self.read_raw_data(self.Z_MSB)

        x, y, z = self.apply_calibration(x, y, z)

        heading = round(self.compute_heading(x,y))

        if relative: # get angle relative to start position
            if 360 >= heading >= self.startPos: 
                angle = heading - self.startPos
            elif 0 <= heading < self.startPos:
                angle = heading + (360 - self.startPos)        
        else:
            angle = heading

        return angle
        
    def apply_calibration(self, raw_x, raw_y, raw_z):
        """
        Apply the offset and scale from calibration to raw readings
        """

        corrected_x = (raw_x - self.X_OFFSET) / self.X_SCALE
        corrected_z = (raw_z - self.Z_OFFSET) / self.Z_SCALE
        corrected_y = (raw_y - self.Y_OFFSET) / self.Y_SCALE
        
        return corrected_x, corrected_y, corrected_z

    def set_home(self, signal=True):
        """
        Set the reference position to read the compass angle from.
        """

        if signal == True:
            self.startPos = self.get_angle(relative=False)

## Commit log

2024-07-05 Created programs for interfacing with components on raspberry pi.
    Main -> Main program for robot. Contains a simple program for obstacle avoidance using ultrasonic sensors and camera.
    tb6612fng -> Module for controlling dc motors using the tb6612fng motor driver module
    tb6612fng_motorDriver_control -> Example program for testing dc motor control with tb6612fng motor driver
    ultrasonicSensor_control -> Module for controlling HCSR04 Ultrasonic Sensors
    pwmControl -> Module for using raspberry pi gpio pins for pwm signals
    [main.py, tb6612fng.py, tb6612fng_motorDriver_control.py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]
2024-07-10 Added Inventor 3D models for Vehicle
    [12v DC motor mount (3D printed).0003.ipt, 12v DC motor mount (3D printed).ipt, 12v DC motor mount.0009.ipt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]
2024-07-10 Deleted unnecessary 3D models
    [12v DC motor mount (3D printed).0003.ipt, 12v DC motor mount (3D printed).ipt, 12v DC motor mount.0009.ipt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]
2024-07-11 Modified steering and added stopper for dirver gear
    [base plate.0031.ipt, base plate.0032.ipt, base plate.ipt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]
2024-07-11 fixed small issue
    [vehicle assembly v2.0059.iam, vehicle assembly v2.0060.iam, vehicle assembly v2.iam]
2024-07-12 Modified the steering
    [driver gear stopper.0002.ipt, driver gear stopper.0003.ipt, driver gear stopper.ipt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]
2024-07-16 Modified model to fit a shorter overall length
    [12v DC motor mount (3D printed).0003.ipt, 12v DC motor mount (3D printed).0004.ipt, 12v DC motor mount (3D printed).ipt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]
2024-07-17 Finalised shorter design and rearranged folders
    [12v DC motor mount (3D printed).0004.ipt, 12v DC motor mount (3D printed).ipt, 12v DC motor mount.0009.ipt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]
2024-07-17 Renamed models to old models
    [12v DC motor mount (3D printed).0003.ipt, 12v DC motor mount (3D printed).ipt, 12v DC motor mount.0009.ipt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]
2024-07-23 Small updates
    [12v DC motor mount (3D printed).0003.ipt, 12v DC motor mount (3D printed).0004.ipt, 12v DC motor mount (3D printed).0006.ipt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]
2024-08-03 Updated Top Plate Model
    [front shaft.0003.ipt, front shaft.0004.ipt, front shaft.ipt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]
2024-08-19 Added outline to engineering journal
    [MONKE_BUST.stl, base plate.0038.ipt, base plate.0039.ipt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]
2024-08-21 Added team parts list
    [Parts List.xlsx]
2024-08-23 Added module for using HMC5883l
    [base plate.0039.ipt, base plate.0040.ipt, base plate.ipt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]
2024-08-26 Refinement of PID code
2024-08-28 PCB images
2024-08-28 Modified front shaft for different set of wheels
    [front shaft v2.0002.ipt, front shaft v2.ipt, front shaft.0005.ipt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]
2024-08-30 Modified camera mount to be angled
    [base plate.0040.ipt, base plate.0041.ipt, base plate.ipt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]
2024-09-03 Updated front shaft and top plate
    [camera mount angled.0004.ipt, camera mount angled.0005.ipt, camera mount angled.ipt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]
2024-09-03 Progress on open challeng and obstacle challenge code
    [calibration_data.csv]
2024-09-04 Competition updates
    [calibration_data.csv]
2024-09-04 Small adjustments to part offsets
    [driver gear adapter v2 with encoder wheel.0004.ipt, driver gear adapter v2 with encoder wheel.0005.ipt, driver gear adapter v2 with encoder wheel.ipt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]
2024-09-05 comp version
    [calibration_data.csv]
2024-11-02 Added ps4 control programs for testing
    [calibration_data.csv, training_data.csv]
2024-11-02 add stl files
    [Vertical Ultrasonic Sensor Mount.stl, ultrasonic and headlight mount.stl]
2024-11-11 Added obstacle and open challenge code with threading.
2024-11-11 Misc changes
    [pyvenv.cfg]
2024-11-12 organise files
    [12v DC motor mount (3D printed).ipt, 12v DC motor mount v2.ipt, 12v DC motor mount.ipt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]
2024-11-12 Delete models/STL files directory
    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
    [Vertical Ultrasonic Sensor Mount.stl, camera mount+HMC angled.stl, ultrasonic and headlight mount.stl]
2024-11-12 Added new robot along with STL files
    [ActuatorLink.ipt, ActuatorLink.stl, Battery Mount V2.0017.ipt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]
2024-11-12 international pcb upload
    [WRO_FE_v4.5.fzz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]
2024-11-12 Rearranged and renamed files
    [training_data.csv]
2024-11-23 Added module for better control of TOF sensors
    [pyvenv.cfg]
2024-11-23 Renamed some files and folders
    [training_data.csv]
2024-11-23 miscellaneous changes
    [calibration_data.csv, training_data.csv]
2024-11-23 Added updated version for Turkiye
    tidied up some files and some CAD changes (new components etc)
    [ActuatorLink.ipt, Battery Mount V2.ipt, Bottom plate.ipt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]
2024-11-24 Minor changes
    [calibration_data.csv]
2024-11-25 Small competition changes
    [calibration_data.csv]
2024-11-26 Competition prep
    [calibration_data.csv]
2024-11-28 Competition changes
    [calibration_data.csv]
